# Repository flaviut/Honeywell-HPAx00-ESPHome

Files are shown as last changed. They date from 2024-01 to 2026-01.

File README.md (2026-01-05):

# ESPHome replacement control board for Honeywell True HEPA Air Purifier.

[Demo of current firmware version](https://youtu.be/eWahNrPkl0M), HPA200_HEPA_Filter_V2.yaml

[Demo of older firmware version](docs/demo.mp4), hepa-filter.yaml
## Current Software Features
Currently the on device firmware recreates all of the factory features of the HPA200 with a few improvements. Connection to Home Assistant is not needed for any functions.
- Fan Speed
  - Pressing the power button will toggle thru the 4 fan speed and then off
  - Turbo button will go to highest fan speed immediately
- Timer
  - Pressing the "Clock" button will toggle thru 2, 4, 8hr run timers
- Filter buttons
  - Current filter life is now show constantly with the LEDs next to the respective buttons. Used life is indicated by color gradient green-yellow-red
  - Filter lifetime hours is configurable in firmware or via Home Assistant
  - Filter usage can be reset by long holding the respective "Check filter" button for 3 seconds
- Dimmer
  - Dimmer setting is now retained even when unplugged. Pressing the dimmer button will cycle between LED levels down to 0%. Pressing any UI button will change all LEDs to max brightness and then they will return to their dimmed values after 5 seconds.
- Home Assistant
  - The fan speed is exposed as a variable speed fan
  - The accumulated filter and prefilter hours are exposed as sensors
  - The filter lifetime values are exposed as Configuration numbers. This allows customization of these values via HA without changes to the firmware.

## Compatibility and Hardware Versions
Compatible with HPA200. It *is not* compatible with the HPA300 or HPA100. The repo title mentioning "HPAx00" is **incorrect**, only the HPA200 will work. The specific PCB design you see in this repo has only been tested in a V2 unit, but is expected to work in V1 units without issue.

I suggest checking compatibility by disassembling your unit and confirming the control panel looks similar and is 205mm between the two furthest apart touch button pads.

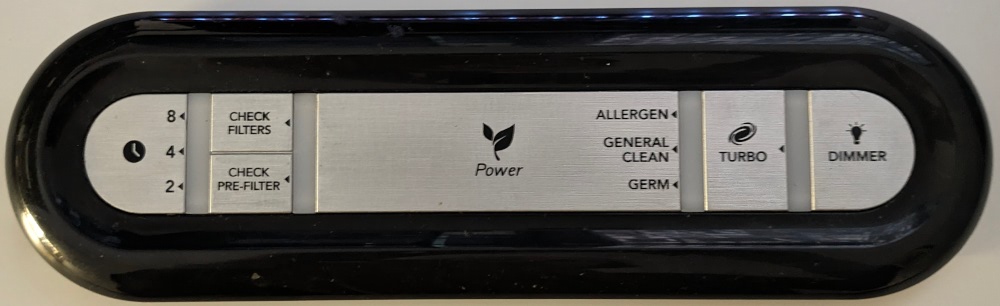
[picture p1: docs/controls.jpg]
control panel photo

### HPA200 Internal PCB Versions
There are two known versions of the the HPA200 internal PCBs V1 and V2. The replacement control PCB is compatible with both of these versions however only the V1 units will need modifications to the power PCB mentioned below.

#### Version 1
EH-A-4200-C V1.00, designed 2012-10-12.
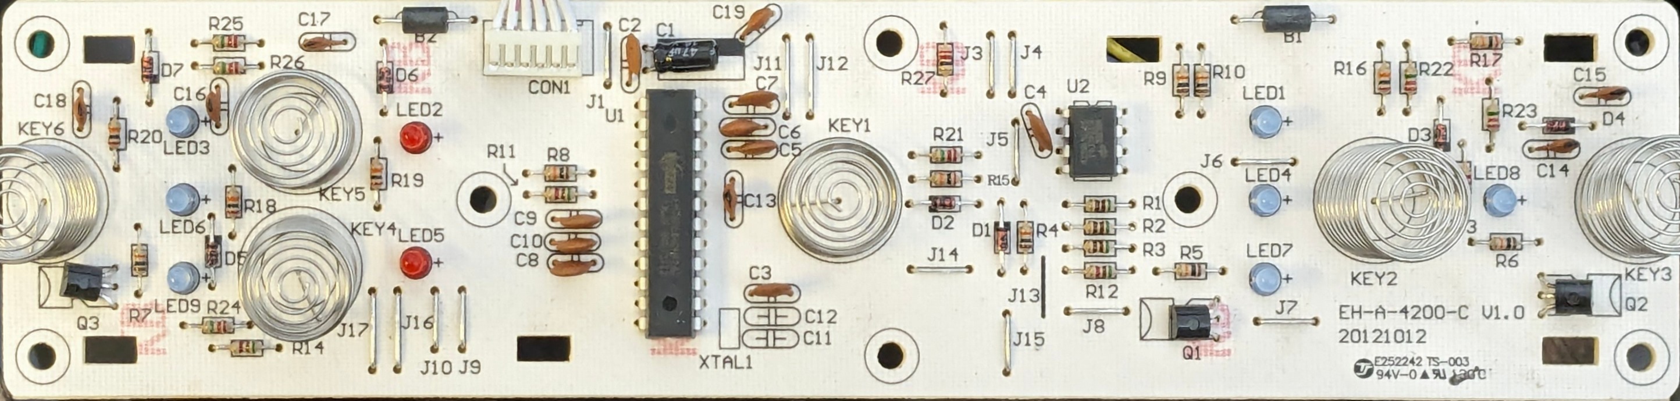
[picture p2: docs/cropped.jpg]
board photo

#### Version 2
EH-A-4200V2-C-V1.0, designed 2019-06-04
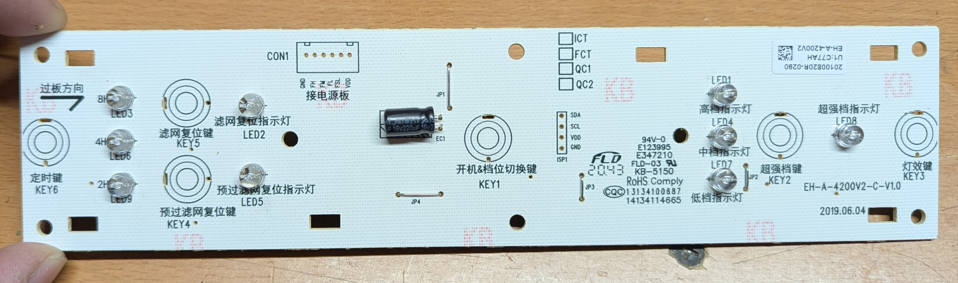
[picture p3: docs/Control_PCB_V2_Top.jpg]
V2 Top

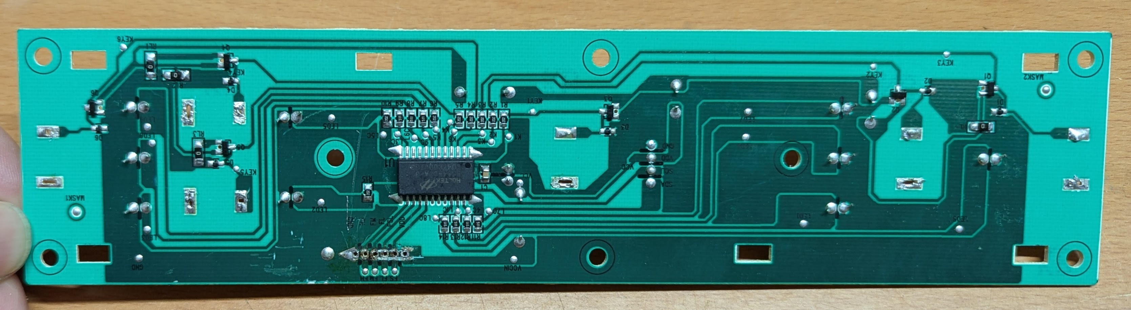
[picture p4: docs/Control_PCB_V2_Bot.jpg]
V2 Bot

## BOM

### Desoldered from original

- 7x touchpad springs
- 1x cable assembly

### Hand-soldered on Control PCB

- 1x [D1 mini ESP32](https://github.com/r0oland/ESP32_mini_KiCad_Library) (Note: this is the 40 pin ESP32 D1 NOT the 20 pin ESP8266 D1 Mini, I used https://www.aliexpress.us/item/2251832671740023.html, "CH9102X drive")
- 1x 6.3V+, 100uF+, P=3.5mm through-hole capacitor (probably optional but needs to be installed on it's side on the top of the PCB or vertical on the bottom due to housing clearance)
- 4x 10-pin 2.54mm headers. 2x of these generally come with your D1 mini ESP32 kit, and you can likely repurpose the long female headers from the kit as the other 2x.

### SMD for Control PCB

- 5x 16V+, 1uF+, 0805 ceramic capacitor
- 10x SKC6812 LEDs
- 1x M7 SMA diode

### Power PCB

There V1 power PCB can not supply enough 5VDC for the ESP and new LEDs. Replacement of the 7805 linear voltage regulator with a modern switched power supply is required.
- 7805-compatible buck regulator module
  - First prototype used https://www.aliexpress.us/item/3256801422436146.html which is no longer listed
  - Currently listed equivalent https://www.aliexpress.us/item/3256807692095306.html
  - Or drop in 7805 replacement IC like this https://www.digikey.com/en/products/detail/xp-power/RBT05W24S05/26667098

The V2 Power PCB has a new 5V power supply that has enough power to support the new control board and no modifications are required.
#### Power PCB Version Images
V1 Power PCB
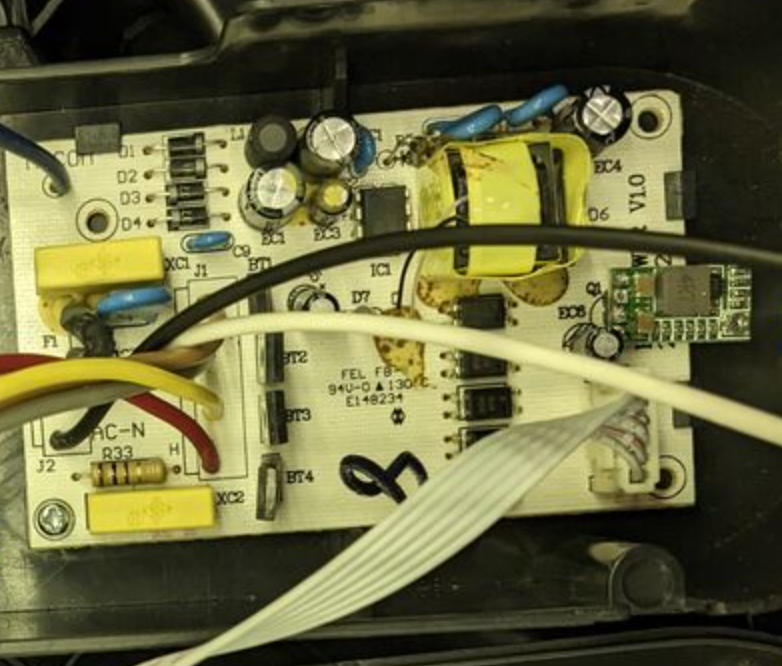
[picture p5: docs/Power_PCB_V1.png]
Power PCB V1

V2 Power PCB
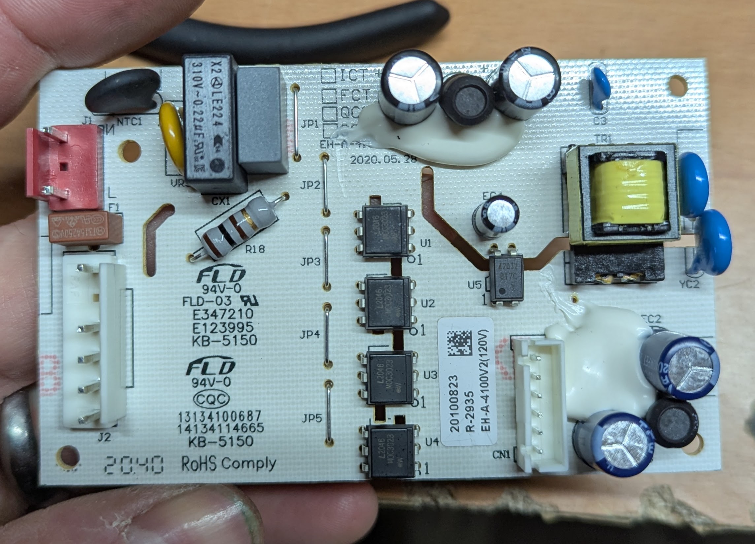
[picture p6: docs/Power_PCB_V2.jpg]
Power PCB V2

## Installation

### PCB Ordering

To the right of this page is the releases area. This area contains all the
materials you need to order your PCB from your preferred board house. I used
JLCPCB, so that is likely easiest, especially if you'd prefer someone else to
do the SMD assembly.

Hand placed SMD and hotplate reflow is also possible. Here is a list of SMD parts from Digikey available as of 2025 Q4. Note these LEDs vary slightly from the ones in the JLC BOM and require a code change.
| Item | DK PN | Qty |
|---|---|---|
| CAP CER 4.7UF 25V X5R 0805 | [1276-1244-1-ND](https://www.digikey.com/en/products/detail/samsung-electro-mechanics/CL21A475KAQNNNE/3886902) | 5 |
| ADDRESS LED DISC SERIAL RGB 1=10 | [1528-1104-ND](https://www.digikey.com/en/products/detail/adafruit-industries-llc/1655/5154679) | 10 |
| DIODE STANDARD 1000V 1A DO214AC | [5399-M7CT-ND](https://www.digikey.com/en/products/detail/shenzhen-slkormicro-semicon-co-ltd/M7/21853078) | 1 |
| CAP ALUM 100UF 20% 16V RADIAL TH | [UVP1C101MPD1TD](https://www.digikey.com/en/products/detail/nichicon/UVP1C101MPD1TD/4328297) | 1 |

### Tools

1. T20 TORX bit, 2in long (V2 units require T20 pin in head security bit)
1. Philips #2 screwdriver
1. Spudger or flathead screwdriver
1. Soldering iron
1. Soldering wick
1. Solder

### Procedure

#### Disassembly

1. Unplug the unit from the wall. If you do not do this, there is a high risk of electric shock.
1. Remove the filter grill from the front of the device by pressing it inwards
1. 6 screw holes will be revealed on the sides of the unit, Unscrew these screws.
    * V1 - 2 of the screws were T20 screws, and the other 4 were #2 philips.
    * V2 - all screws are T20 pin in head security bit
1. The top of the unit still has four clips holding the front on. Use a spudger to release the top clips on the front side.
1. Remove the front panel of the unit.
1. 4 smaller philips screws will be revealed holding the top on. Unscrew these.
1. Use a spudger to release the top clips on the back side.
1. The top panel should easily come off.
1. Unscrew the screws holding the controls tray.
1. Unscrew the screws holding the control PCB.
1. Release the clips holding the control PCB in.
1. Unplug the control cable assembly from the power supply board.
1. Use the soldering iron and solder wick to remove the touchpad springs and the cable assembly.

#### Modifications

**Figure 1:**

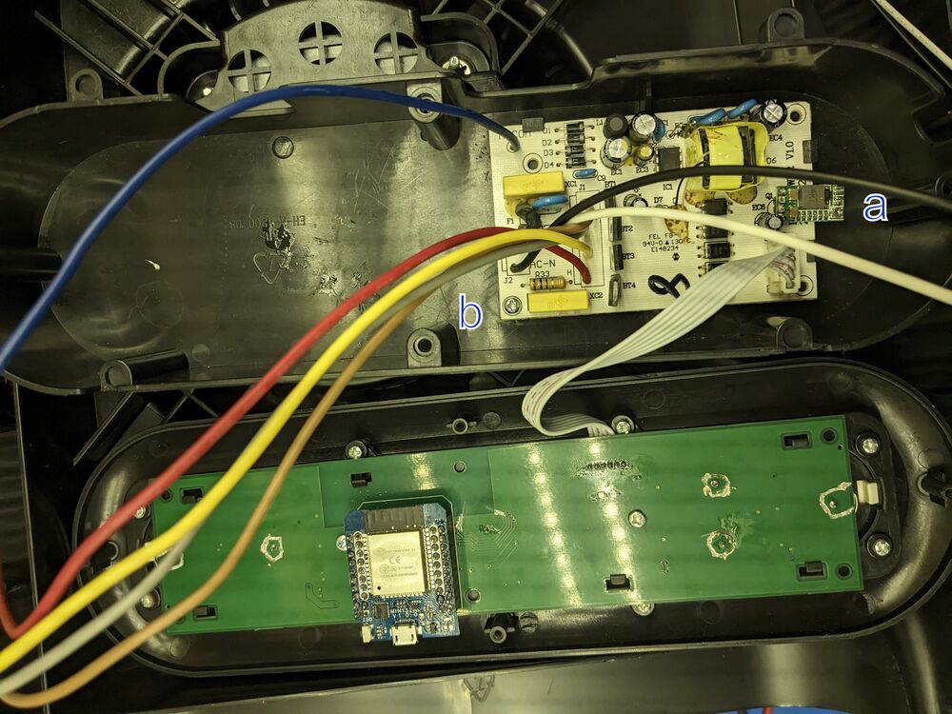
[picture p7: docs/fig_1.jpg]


1. Flash the D1 mini ESP32 with ESPHome via the USB port. See the config at [HPA200_HEPA_Filter_V2.yaml](HPA200_HEPA_Filter_V2.yaml) as a starting point.
1. Solder the touchpad springs on the top side of the replacement control board. This is the side of the control board with the LEDs.
1. Solder the cable assembly on the top side of the replacement control board.
1. Solder the D1 mini ESP32 on the reverse of the replacement control board, using the silk-screen outline as a guide.
1. **V1 Power supply boards only:** De-solder Q1 from the power-supply board. Replace it with a 7805-compatible buck regulator. The output pin is the one closest to the connector. (see Fig 1, a)
1. Re-install the power supply board. Note that the screw is flat-tipped and shorter than the others (Fig 1, b)
1. Insert the board into the control panel and reinstall all screws.

#### Re-assembly

**Figure 2:**

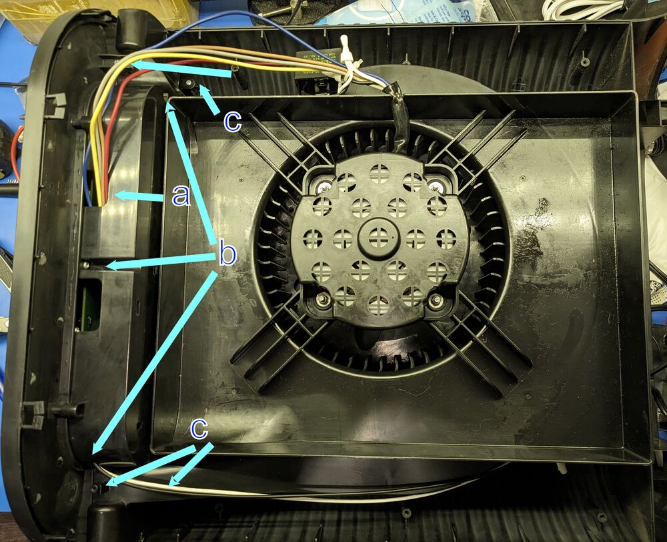
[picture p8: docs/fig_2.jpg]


**Figure 3:**

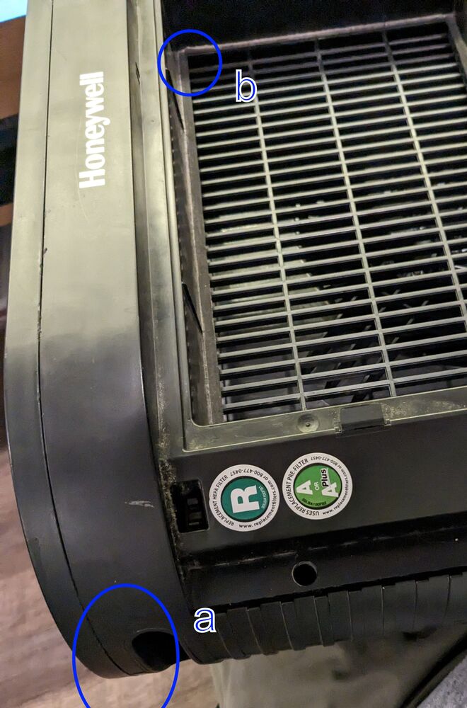
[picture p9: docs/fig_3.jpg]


Reverse steps to re-assemble. Some notes:

1. Make sure the motor wires are coming out of the hole indicated in Fig 2, a
1. First screw the electronics box to the lid (Fig 2, b)
1. Then screw the lid onto the rest of the unit (Fig 2, c)
1. When snapping the front of the device on, make sure the plastic next to the handle (Fig 3, a) is correctly snapped in on both sides

## Software

See the config at [hepa-filter.yaml](./hepa-filter.yaml) as a starting point. You will need to use ESP32 Touch Pad's `setup_mode` to calibrate touch thresholds for each unit variance between units can be large.

## Credits

- Thank you to [Keith Burzinski](https://github.com/kbx81) for reviewing my design through endless revisions!

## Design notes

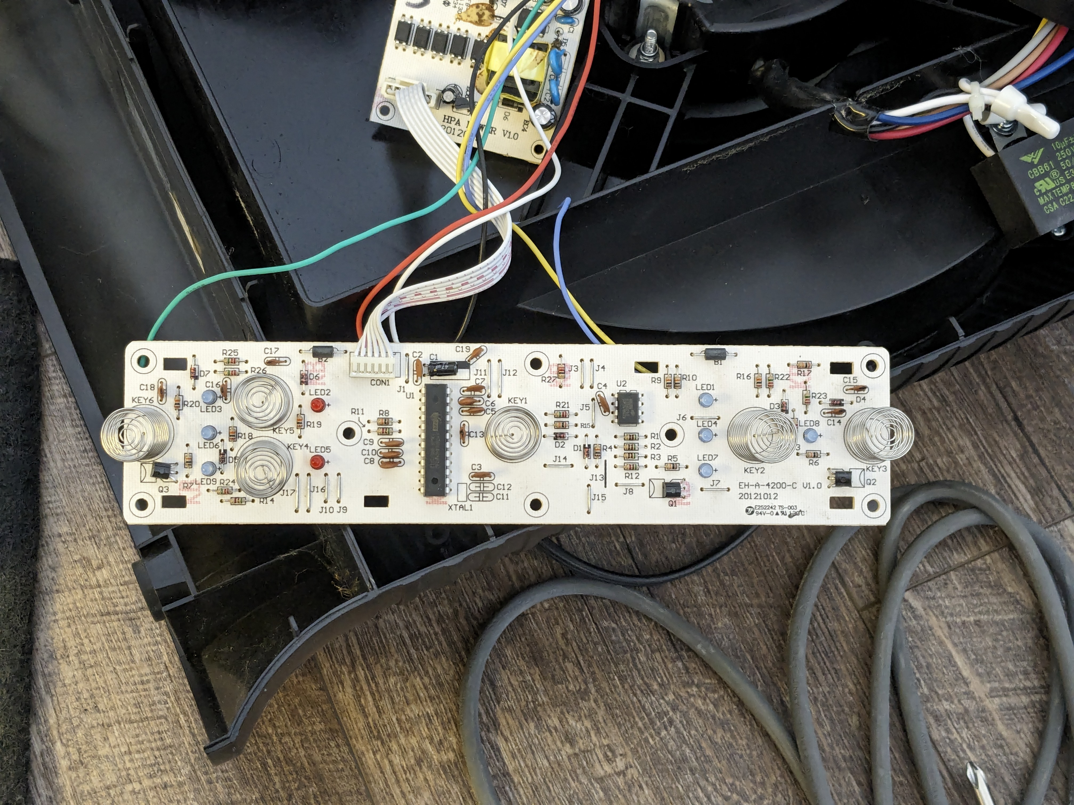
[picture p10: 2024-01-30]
docs/photo.jpg

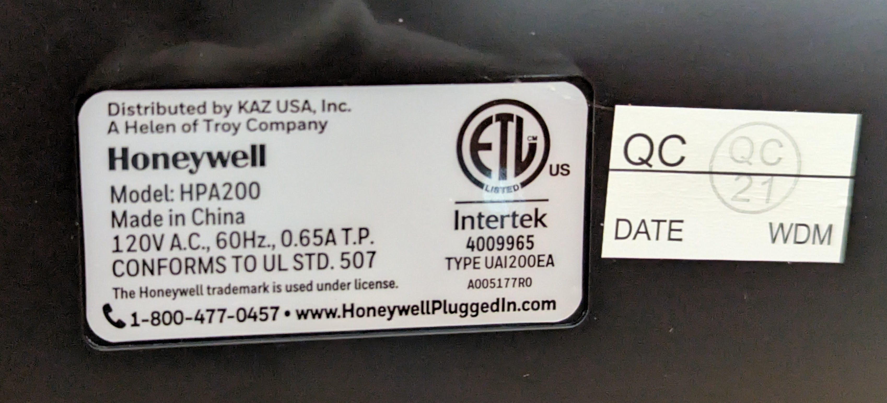
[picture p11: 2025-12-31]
docs/Device_label_V2.jpg

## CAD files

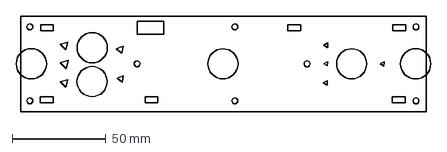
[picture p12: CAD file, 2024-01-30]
fan-BodySketch.dxf
220.9 x 50.8 mm

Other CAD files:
fan.FCStd

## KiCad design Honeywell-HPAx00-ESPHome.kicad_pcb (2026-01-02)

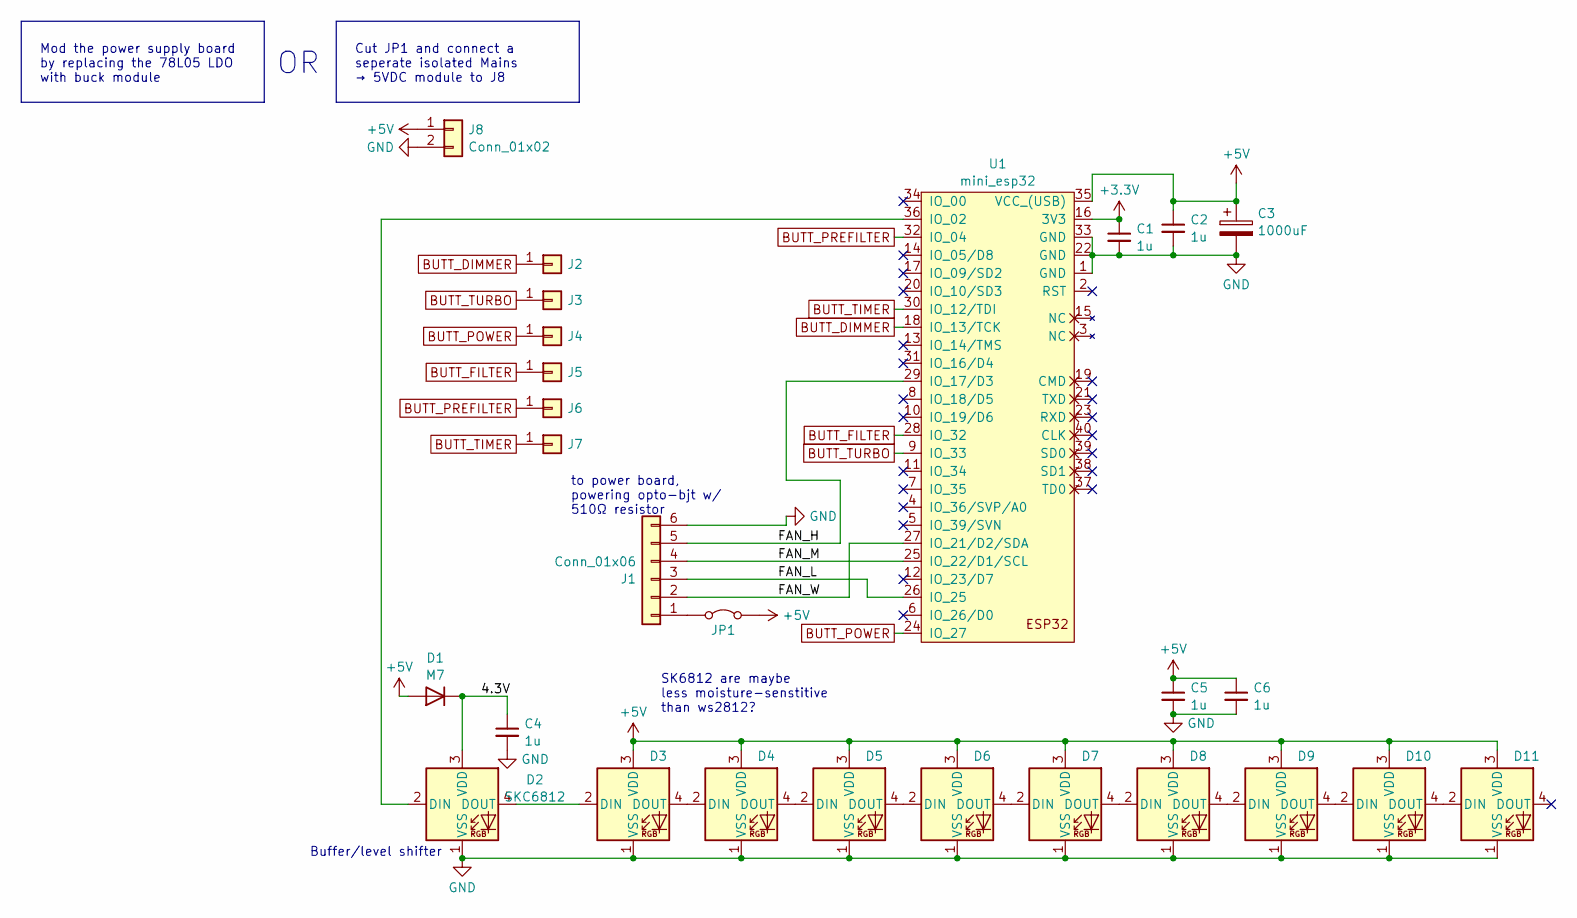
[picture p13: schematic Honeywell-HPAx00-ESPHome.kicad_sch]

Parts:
C1, C2, C4, C5, C6: 1u; C_0805_2012Metric_Pad1.18x1.45mm_HandSolder; LCSC C1779
C3: 1000uF; CP_Radial_D8.0mm_P3.50mm; LCSC C494544
D1: M7; D_SMA_Handsoldering; LCSC C95872
D2, D3, D4, D5, D6, D7, D8, D9, D10, D11: SKC6812; LED_SK6812_PLCC4_5.0x5.0mm_P3.2mm; LCSC C2890040
J1: Conn_01x06; JST_PH_S6B-PH-K_1x06_P2.00mm_Horizontal
J2, J3, J4, J5, J6, J7: Conn_01x01; Honeywell V1+2 Spring
J8: Conn_01x02; SolderWire-0.5sqmm_1x02_P4.6mm_D0.9mm_OD2.1mm_Relief
JP1: Jumper_2_Bridged; SolderJumper-2_P1.3mm_Bridged_RoundedPad1.0x1.5mm
U1: mini_esp32; ESP32_mini

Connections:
+3.3V: C1.1, U1.16 (3V3)
+5V: C2.1, C3.1, C5.1, C6.1, D1.2 (A), D3.3 (VDD), D4.3 (VDD), D5.3 (VDD), D6.3 (VDD), D7.3 (VDD), D8.3 (VDD), D9.3 (VDD), D10.3 (VDD), D11.3 (VDD), J8.1, JP1.2 (B), U1.35 (VCC_(USB))
/4.3V: C4.1, D1.1 (K), D2.3 (VDD)
/FAN_H: J1.5, U1.29 (IO_17/D3)
/FAN_L: J1.3, U1.26 (IO_25)
/FAN_M: J1.4, U1.25 (IO_22/D1/SCL)
/FAN_W: J1.2, U1.27 (IO_21/D2/SDA)
BUTT_DIMMER: J2.1, U1.18 (IO_13/TCK)
BUTT_FILTER: J5.1, U1.28 (IO_32)
BUTT_POWER: J4.1, U1.24 (IO_27)
BUTT_PREFILTER: J6.1, U1.32 (IO_04)
BUTT_TIMER: J7.1, U1.30 (IO_12/TDI)
BUTT_TURBO: J3.1, U1.9 (IO_33)
GND: C1.2, C2.2, C3.2, C4.2, C5.2, C6.2, D2.1 (VSS), D3.1 (VSS), D4.1 (VSS), D5.1 (VSS), D6.1 (VSS), D7.1 (VSS), D8.1 (VSS), D9.1 (VSS), D10.1 (VSS), D11.1 (VSS), J1.6, J8.2, U1.1 (GND), U1.22 (GND), U1.33 (GND)
unnamed: D2.2 (DIN), U1.36 (IO_02)
unnamed: D2.4 (DOUT), D3.2 (DIN)
unnamed: D3.4 (DOUT), D4.2 (DIN)
unnamed: D4.4 (DOUT), D5.2 (DIN)
unnamed: D5.4 (DOUT), D6.2 (DIN)
unnamed: D6.4 (DOUT), D7.2 (DIN)
unnamed: D7.4 (DOUT), D8.2 (DIN)
unnamed: D8.4 (DOUT), D9.2 (DIN)
unnamed: D9.4 (DOUT), D10.2 (DIN)
unnamed: D10.4 (DOUT), D11.2 (DIN)
unnamed: J1.1, JP1.1 (A)

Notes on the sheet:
Cut JP1 and connect a seperate isolated Mains → 5VDC module to J8
Buffer/level shifter
SK6812 are maybe less moisture-senstitive than ws2812?
to power board, powering opto-bjt w/ 510Ω resistor
Mod the power supply board by replacing the 78L05 LDO with buck module

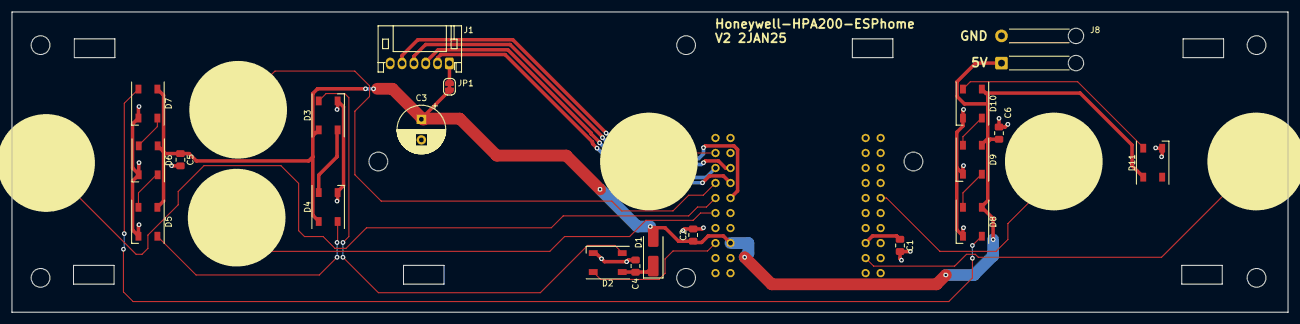
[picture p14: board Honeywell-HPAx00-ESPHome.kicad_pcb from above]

Board: 2 copper layers, 215.9 x 50.8 mm, 27 parts (1 on the bottom side), 25 nets.

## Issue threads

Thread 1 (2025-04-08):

HPA300 not compatible

blouphil, 2025-04-08:
Hi there,

I might be a bit late to the game, but getting ESPHome working with the HPA300 has been on my wishlist for a while—so I was really excited to come across your project. I recently ordered the boards and got started, but ran into an issue: unfortunately, the stock board in my unit is longer than the one provided in this repo (24.5cm vs 21.5cm):

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

Additionally, the power supply setup appears to be different:

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

A couple of questions/suggestions:

- Would it be possible to get a Gerber file version that matches the dimensions of this board revision? I’d love to contribute, but I don’t have the skills to design a new one from scratch.

- It might also be helpful to update the documentation to reflect that the HPA300 may not be compatible with the current hardware layout, at least for some units.

Thanks again for all your work—really appreciate it!

flaviut, 2025-04-08:
I'll update the main page to indicate there are multiple models.

I think the new power supply may be a problem. Can you take a top-down image of it, front & back?

I'm certain you could adapt the board yourself in KiCad if you gave it a try. You wouldn't need to change the circuit, just the PCB layout, and KiCad has a "design rule check" that makes sure you haven't made any mistakes.

flaviut, 2025-04-08:
Oh, and if you could take a picture of the outside/any serial number labels on your unit, I'd also appreciate that! If there's a way to check for compatibility without  opening it up that would be really nice.

blouphil, 2025-04-09:
Here's the tag from the bottom of the unit; I don't see any serial number but there's a model number (_HPA300CV2_):

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
Could the "C" be for the Canadian version?

Power supply shots:

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

There's a +5V there not too far from CN1, perhaps we could use it?

As for KiCad, I'm feeling a bit overwhelmed trying to expand the PCB layout. I think I managed to extend the board, but then all the layers got messy, I'll try again.

flaviut, 2025-04-09:
> HPA200CV2

Canadian, but I think the V2 is likely the more relevant part. Mine is just "HPA200". I'll update the doc tomorrow.

> There's a +5V there not too far from CN1, perhaps we could use it?

Yup! 5V also is fed onto CN1, so it can be used from there.

I am a bit concerned about the new power supply. The old one needed some modification before it could provide enough power for the ESP32. The new power supply looks more efficient, but I'd still test it out before going through the effort of editing the PCB. I suggest one of these approaches:

- hooking up an esp32 between 5V & GND (GND text is mirrored on the board) and testing an esphome remote software update, since that is likely to be a large power draw.
- for a worst-case test, hook up a 10Ω resistor between 5V & GND and measure the output voltage. You'll need to be quick, the resistor will get very hot very fast: 2.5W dissipated; you may need several larger resisters in parallel.

Be careful of the mains voltage on this board. It can be deadly, do not touch the board while plugged in.

> As for KiCad, I'm feeling a bit overwhelmed trying to expand the PCB layout

Sorry! It's easy to forget what it's like being new to something like this :)

Good luck, and there's lots of great tutorials out there. The refill zones button & measure tool will be your best friends for this board.

blouphil, 2025-04-09:
If anyone’s looking for a blank PCB for HPA200, I’ve got a few extras I’d be happy to share. Just let me know!

blouphil, 2025-04-30:
Small update: I’ve acquired both an HPA100 and HPA200, in addition to my original HPA300.

With the custom PCB placed on top of each model, it's clear that only the HPA200 (version 1) is compatible:

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

I was able to get the HPA200CV1 working with the PCB included in this repo. Most functionality is working fine, but I’ve noticed the following issues:

- The power supply barely provides enough current to power even a single LED—this was somewhat expected. Could we consider adding a secondary AC-to-DC power supply inside the unit and cutting the traces from the original 5V input?

- I had to cut the traces for two touch pads that weren’t functioning. It’s possible the PCB was using invalid GPIOs. After making changes, I connected:

1. `prefilter` to `GPIO13 (TCK)`
2. `dimmer` to `GPIO4`

With these changes, both touch buttons are now working as expected.

flaviut, 2025-04-30:
> Small update: I’ve acquired both an HPA100 and HPA200, in addition to my original HPA300.
>
> With the custom PCB placed on top of each model, it's clear that only the HPA200 (version 1) is compatible:

Thank you for your research, I've updated the readme.

> Could we consider adding a secondary AC-to-DC power supply inside the unit and cutting the traces from the original 5V input?

absolutely possible! I updated the PCB with 71892ccbd5a701d998b2bd5a68c1bdf5b202a5c6, but I don't have mine open so I'm not sure what the required dimensions for the power supply would be. Even without a redesign, it should be easy to cut the 5V wire on the PCB and scrape off the resist to solder wires for the new PSU.

> I had to cut the traces for two touch pads that weren’t functioning. It’s possible the PCB was using invalid GPIOs. After making changes, I connected:

Fixed that in the pcb design too, but I only moved prefilter to gpio4 since that seemed simplest: d52fe1105f7c50b1585c5bcc252ec893c46907e7

Closed 2025-04-30.

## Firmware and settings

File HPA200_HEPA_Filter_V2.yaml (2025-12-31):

substitutions:
  # https://esphome.io/guides/configuration-types.html#substitutions
  device_name: hepa-filter # hostname & entity_id
  friendly_name: HEPA Filter # Displayed in HA frontend
  filter_life: "1200" #hours
  prefilter_life: "300" #hours
  touch_threshold_timer: "2520"
  touch_threshold_dimmer: "3000"
  touch_threshold_prefilter: "3019"
  touch_threshold_filter: "2376"
  touch_threshold_turbo: "3722"
  touch_threshold_power: "2430"
  touch_setup_mode: "false" # https://esphome.io/components/binary_sensor/esp32_touch/

esphome:
  name: ${device_name}
  name_add_mac_suffix: true
  friendly_name: ${friendly_name}

  on_boot:
    - light.turn_on:
        id: status_light
        effect: "Rainbow Wave"
    - delay: 2s
    - light.turn_off:
        id: status_light
        transition_length: 1s
    - lambda: |-
        // Initialize interaction time so auto-dim kicks in after boot
        id(last_interaction_time) = millis();

esp32:
  board: nodemcu-32s

logger:

# Enable Home Assistant API
api:

# Allow Over-The-Air updates
ota:
  platform: esphome

wifi:
  ssid: !secret wifi_ssid
  password: !secret wifi_password

light:
  - platform: neopixelbus
    type: GRB
    variant: WS2811
    pin: GPIO2
    num_leds: 10
    id: status_light
    name: led_strip
    internal: True
    effects:
      - addressable_rainbow:
          name: "Rainbow Wave"
          speed: 10
          width: 50

# LED locations
#0 under power button
#1 check filter
#2 check pre filter
#3 timer "2" bottom
#4 timer  "4" middle
#5 timer "8" top
#6 Fan "Germ" bottom
#7 fan "general clean" middle
#8 fa "allergen" top
#9 turbo

esp32_touch:
  setup_mode: ${touch_setup_mode}
  voltage_attenuation: 1.5V
  iir_filter: 100ms

binary_sensor:
  - platform: esp32_touch
    threshold: ${touch_threshold_timer}
    pin: GPIO12
    id: timer
    on_press:
      then:
        - lambda: |-
            id(last_interaction_time) = millis();
            id(leds_dimmed) = false;
            // Cycle: 0 -> 2 -> 4 -> 8 -> 0
            int current = id(timer_hours);
            if (current == 0) {
              id(timer_hours) = 2;
            } else if (current == 2) {
              id(timer_hours) = 4;
            } else if (current == 4) {
              id(timer_hours) = 8;
            } else {
              id(timer_hours) = 0;
            }
            // Set end time
            if (id(timer_hours) > 0) {
              id(timer_end_time) = millis() + (id(timer_hours) * 3600000UL);
            } else {
              id(timer_end_time) = 0;
            }
  - platform: esp32_touch
    threshold: ${touch_threshold_dimmer}
    pin: GPIO13
    id: dimmer
    on_press:
      then:
        - lambda: |-
            // Cycle through dim levels: 0.35 -> 0.70 -> 1.00 -> 0.00
            float current_level = id(stored_dim_level);
            
            if (current_level < 0.2) { // Was 0.0
               id(stored_dim_level) = 0.35;
            } else if (current_level < 0.5) { // Was 0.35
               id(stored_dim_level) = 0.70;
            } else if (current_level < 0.85) { // Was 0.70
               id(stored_dim_level) = 1.0;
            } else { // Was 1.0
               id(stored_dim_level) = 0.0;
            }
            
            // Force "dimmed" state and show preview immediately
            id(leds_dimmed) = true;
            id(current_brightness) = id(stored_dim_level);
            // Do NOT reset last_interaction_time so it stays in this preview state
  - platform: esp32_touch
    threshold: ${touch_threshold_prefilter}
    pin: GPIO4
    id: prefilter
    on_multi_click:
      - timing:
          - ON for at least 3s
        then:
          - lambda: |-
              id(prefilter_hours) = 0.0;
              id(last_interaction_time) = millis();
              id(leds_dimmed) = false;
    on_press:
      then:
        - lambda: |-
            id(last_interaction_time) = millis();
            id(leds_dimmed) = false;
  - platform: esp32_touch
    threshold: ${touch_threshold_filter}
    pin: GPIO32
    id: filter
    on_multi_click:
      - timing:
          - ON for at least 3s
        then:
          - lambda: |-
              id(filter_hours) = 0.0;
              id(last_interaction_time) = millis();
              id(leds_dimmed) = false;
    on_press:
      then:
        - lambda: |-
            id(last_interaction_time) = millis();
            id(leds_dimmed) = false;
  - platform: esp32_touch
    threshold: ${touch_threshold_turbo}
    pin: GPIO33
    id: turbo
    on_press:
      then:
        - lambda: |-
            id(last_interaction_time) = millis();
            id(leds_dimmed) = false;
        - fan.turn_on:
            id: my_fan
            speed: 4
  - platform: esp32_touch
    threshold: ${touch_threshold_power}
    pin: GPIO27
    id: power
    on_press:
      then:
        - lambda: |-
            id(last_interaction_time) = millis();
            id(leds_dimmed) = false;
        - fan.cycle_speed:
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

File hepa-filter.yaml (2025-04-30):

substitutions:
  # https://esphome.io/guides/configuration-types.html#substitutions
  device_name: hepa-filter # hostname & entity_id
  friendly_name: HEPA Filter # Displayed in HA frontend

esphome:
  name: ${device_name}
  on_boot:
  - light.turn_on:
      id: status_light
      transition_length: 0s
      red: 0
      green: .1
      blue: 0
      white: 0
  - light.addressable_set:
      id: status_light
      red: 0
      green: 0
      blue: 0

esp32:
  board: nodemcu-32s

logger:

# Enable Home Assistant API
api:
  encryption:
    key: !secret api_key
# enable ota updates
ota: {password: !secret api_password}

wifi:
  ssid: !secret wifi_ssid
  password: !secret wifi_password

light:
  - platform: esp32_rmt_led_strip
    rgb_order: GRB
    pin: GPIO2
    num_leds: 10
    rmt_channel: 1
    chipset: SK6812
    is_rgbw: true
    id: status_light
    internal: true

esp32_touch:
  setup_mode: false
  voltage_attenuation: 1.5V
  iir_filter: 100ms

binary_sensor:
  - platform: esp32_touch
    threshold: 2050
    pin: GPIO12
    id: timer
  - platform: esp32_touch
    threshold: 2550
    pin: GPIO13
    id: dimmer
  - platform: esp32_touch
    threshold: 2480
    pin: GPIO4
    id: prefilter
  - platform: esp32_touch
    threshold: 2210
    pin: GPIO32
    id: filter
  - platform: esp32_touch
    threshold: 3117
    pin: GPIO33
    id: turbo
    on_press:
      then:
        - fan.turn_on:
            id: my_fan
            speed: 4
  - platform: esp32_touch
    threshold: 2207
    pin: GPIO27
    id: power
    on_press:
      then:
      - fan.cycle_speed:
          id: my_fan
          off_speed_cycle: true


switch:
  - platform: gpio
    pin: GPIO21
    id: fan_low
    interlock_wait_time: 250ms
    interlock: &interlock_group [fan_low, fan_mid, fan_high, fan_turbo]
  - platform: gpio
    pin: GPIO25
    id: fan_mid
    interlock_wait_time: 250ms
    interlock: *interlock_group
  - platform: gpio
    pin: GPIO22
    id: fan_high
    interlock_wait_time: 250ms
    interlock: *interlock_group
  - platform: gpio
    pin: GPIO17
    id: fan_turbo
    interlock_wait_time: 250ms
    interlock: *interlock_group
output:
  - platform: template
    id: fan_speed_output
    type: float
    write_action:
      - lambda: |-
          id(fan_low).turn_off();
          id(fan_mid).turn_off();
          id(fan_high).turn_off();
          id(fan_turbo).turn_off();
          auto light = ((AddressableLight*)id(status_light).get_output());
          for (int i = 6; i <= 9; i++) {
            light->get(i).set(Color::BLACK);
          }

          if (state < 0.24) {
          } else if (state < 0.26) {
            id(fan_low).turn_on();
            light->get(6).set(Color(255,0,0,0));
          } else if (state < 0.51) {
            id(fan_mid).turn_on();
            light->get(7).set(Color(255,0,0,0));
          } else if (state < 0.76) {
            id(fan_high).turn_on();
            light->get(8).set(Color(255,0,0,0));
          } else {
            id(fan_turbo).turn_on();
            light->get(9).set(Color(255,0,0,0));
          }
          light->schedule_show();

fan:
  - platform: speed
    name: "Filter Speed"
    output: fan_speed_output
    speed_count: 4
    id: my_fan

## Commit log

2024-01-30 Update based on feedback
    [Honeywell-HPAx00-ESPHome.kicad_pcb, Honeywell-HPAx00-ESPHome.kicad_sch, hp-air-filter.kicad_pcb]
2024-01-31 Update design
    [Honeywell-HPAx00-ESPHome.kicad_pcb, Honeywell-HPAx00-ESPHome.kicad_sch]
2024-02-04 final tweaks
    [Honeywell-HPAx00-ESPHome.kicad_pcb, Honeywell-HPAx00-ESPHome.kicad_sch]
2024-02-21 Fix issues from production
    1. clear space around buttons on ground plane
    2. increase capacitor to 4.7mF (1mF would be an absolute minimum)
    3. increase hole size for connector, since it's a very tight fit
    [Honeywell-HPAx00-ESPHome.kicad_pcb, Honeywell-HPAx00-ESPHome.kicad_sch]
2024-02-22 Update with complete instructions
    [Honeywell-HPAx00-ESPHome.kicad_pcb, Honeywell-HPAx00-ESPHome.kicad_sch]
2024-02-22 Add PCB instructions
2025-04-10 T20 bit
    Removed security, since T20 TORX security has an actual pin in the center. These are regular T20 TORX screws.
2025-04-30 Add connector for extra 5V PSU
    [Honeywell-HPAx00-ESPHome.kicad_pcb, Honeywell-HPAx00-ESPHome.kicad_sch]
2025-04-30 Move prefilter to GPIO4 (#1)
    [Honeywell-HPAx00-ESPHome.kicad_pcb, Honeywell-HPAx00-ESPHome.kicad_sch]
2025-12-30 Major updates to readme, new device yaml, documentation of V2 hardware, light file organization.
2026-01-02 Updated PCB with new spring footprints
    [Honeywell-HPAx00-ESPHome.kicad_pcb, Honeywell-HPAx00-ESPHome.kicad_sch]
2026-01-05 Revise demo links in README.md
    Added YT link to current FW demo
